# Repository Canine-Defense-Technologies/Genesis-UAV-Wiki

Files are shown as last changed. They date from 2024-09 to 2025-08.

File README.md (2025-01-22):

---
cover: .gitbook/assets/23155555555.png
coverY: 0
---

# Overview

## Genesis UAV

{% embed url="https://youtu.be/HFgrlNx3w98?feature=shared" %}

The merge between an FPV drone and a slow-moving high-endurance drone platform Genesis defines a new family of Tactical Utility Drones. The true balance of agility, speed, endurance, modularity, & manufacturability; Genesis is a new drone class. Built for serious U.S. civilians & defense professionals.

{% hint style="info" %}
Genesis drone family and all associated files on this wiki © 2025 by [Canine Defense Technologies ](https://www.k9defense.tech/)is licensed under [CC BY-SA 4.0](https://creativecommons.org/licenses/by-sa/4.0/?ref=chooser-v1)
{% endhint %}

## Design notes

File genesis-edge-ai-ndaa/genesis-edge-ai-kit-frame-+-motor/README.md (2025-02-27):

---
cover: ../../.gitbook/assets/P1170314.JPG
coverY: -83
---

# Genesis Edge AI Kit (Frame + Motor)

## Purchase Kit Here:

{% embed url="https://www.k9defense.tech/store/p/genesis-full-hardware-kit-j2g47-s429t-xrbjd" %}

<figure><figcaption></figcaption></figure>

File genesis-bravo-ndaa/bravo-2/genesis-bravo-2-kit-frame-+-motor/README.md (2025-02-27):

# Copy of Genesis Bravo 2 Kit (Frame + Motor)

## Purchase Kit Here:

{% embed url="https://www.k9defense.tech/store/p/genesis-full-hardware-kit-j2g47-s429t" %}

<figure><figcaption></figcaption></figure>

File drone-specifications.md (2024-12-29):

---
cover: .gitbook/assets/32467456.png
coverY: 0
---

# Drone Specifications

{% hint style="info" %}
The specifications will vary based on setup, motor selection, battery selection, frame type, etc. The metrics below should only be used for reference.&#x20;
{% endhint %}

| Stat | Value | Freedom Units |
| --- | --- | --- |
| Airframe Weight | 1.8 kg (Carbon Fiber)  | 2.2 lbs |
| Airframe Weight with Battery | 2.65 kg (Carbon Fiber) | 5.8 lbs |
| Blade Diameter | 15" \~ 20" | 15" \~ 20" |
| Flight Time | 15 \~ 40+ min | 15 \~ 40+ min |
| Max speed | 100+ km/hr | 62+ mph |
| Climb Rate | 16 m/sec | 35.7 mph |
| Thrust to Weight Ratio | 6.1/1 | 6.1/1 |
| Max Payload | 4 kg | 8.8 lbs |
| Do Not Exceed Payload | 5 kg | 11 lbs |
| Nominal Payload | 2 kg | 4.4 lbs |

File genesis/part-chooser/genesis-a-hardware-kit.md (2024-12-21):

---
cover: ../../.gitbook/assets/20241018_020027 (1).jpg
coverY: 0
---

# Genesis Hardware Kit (Archived)

{% hint style="warning" %}
As of Dec 2024, this page is stored for archival purposes. K9 is no longer offering this product.
{% endhint %}

## Purchase Kit Here:

{% embed url="https://www.k9defense.tech/store/p/genesis-hardware-kit" %}

We've made it a convenient kit with all the major hardware pre-labeled and sourced. The kit also includes the TPU landing gear, so you will only need to print the rest of the frame in one material.

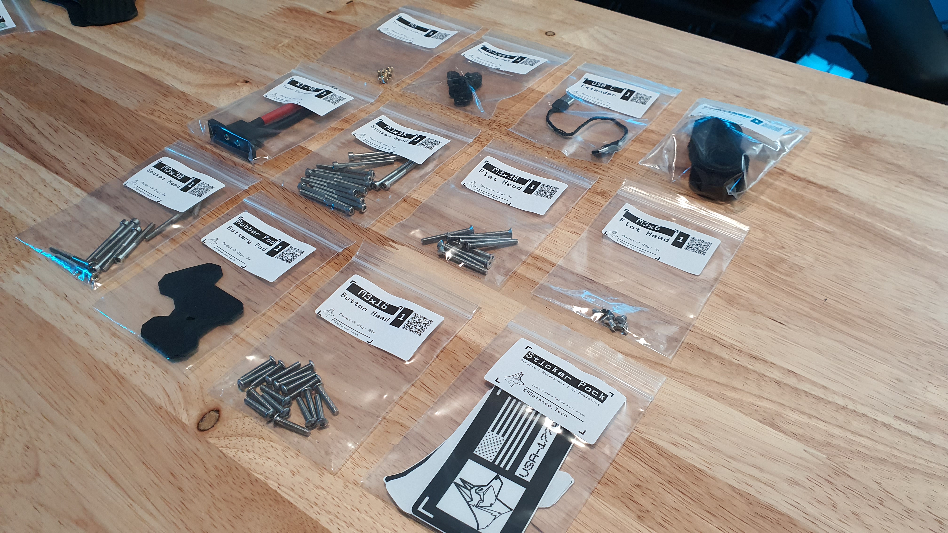
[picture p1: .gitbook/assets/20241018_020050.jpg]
<figure><figcaption></figcaption></figure>

{% hint style="info" %}
After purchasing the kit, ensure to source the additional parts.
{% endhint %}

## Additional Parts to Source:&#x20;

{% content-ref url="3d-printed-parts/" %}
[3d-printed-parts](3d-printed-parts/)
{% endcontent-ref %}

{% content-ref url="hardware/sheet-parts.md" %}
[sheet-parts.md](hardware/sheet-parts.md)
{% endcontent-ref %}

{% content-ref url="hardware/propellers.md" %}
[propellers.md](hardware/propellers.md)
{% endcontent-ref %}

{% content-ref url="hardware/arm-tubes.md" %}
[arm-tubes.md](hardware/arm-tubes.md)
{% endcontent-ref %}

{% content-ref url="electronics/" %}
[electronics](electronics/)
{% endcontent-ref %}

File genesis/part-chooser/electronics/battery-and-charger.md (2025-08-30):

---
cover: ../../../.gitbook/assets/1342234.png
coverY: 0
---

# Battery

{% hint style="warning" %}
As of April 2025, this page is stored for archival purposes. K9 has replaced the Genesis drone family to the newly improved Genesis Bravo 3.
{% endhint %}

### Reccomended Batteries:

| Part | Capacity  | C Rating | Link | Notes |
| --- | --- | --- | --- | --- |
| RDQ 6s | 6000 mah  | 100c | [Link](https://www.racedayquads.com/collections/6s-batteries/products/rdq-series-22-2v-6s-6000mah-100c-lipo-battery-xt90-anti-spark) | Best value. |
| Gens Ace 6s | 5500 mah  | 60c | [Link](https://genstattu.com/GA-B-60C-5500-6S1P-XT90S) | |
| Tattu G-Tech 6s | 11000 mah | 25c | [Link](https://genstattu.com/tattu-22-8-25c-6s-11000-mah-high-voltage-lipo-battery-with-xt90-s-plug-for-uav.html) | |

{% hint style="info" %}
When choosing alternative batteries, it is reccomended to use a 6S battery for Genesis. Ensure that there is a minimum C rating of 20c, and a minimum capacity of 3000 mah.&#x20;
{% endhint %}

### Battery Straps:

| Part | Link | Notes |
| --- | --- | --- |
| | [Link](https://www.racedayquads.com/collections/6s-batteries/products/rdq-series-22-2v-6s-6000mah-100c-lipo-battery-xt90-anti-spark) | Best value. |
| Gens Ace 6s | [Link](https://genstattu.com/GA-B-60C-5500-6S1P-XT90S) | |
| Tattu G-Tech 6s | [Link](https://genstattu.com/tattu-22-8-25c-6s-11000-mah-high-voltage-lipo-battery-with-xt90-s-plug-for-uav.html) | |

### Reccomended LiPo Fireproof Bags & Boxes:

{% hint style="warning" %}
Fireproof bags are **HIGHLY** recommended for charging and transporting LiPo batteries.
{% endhint %}

{% embed url="https://store.flitetest.com/flite-test-lipo-bag/" %}

{% embed url="https://store.flitetest.com/bat-safe-lipo-charging-box/" %}

### Learn more about choosing batteries for drones:

{% embed url="https://oscarliang.com/lipo-battery-guide/" %}

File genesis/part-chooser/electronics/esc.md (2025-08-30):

---
cover: ../../../.gitbook/assets/43543.png
coverY: 0
---

# ESC

{% hint style="warning" %}
As of April 2025, this page is stored for archival purposes. K9 has replaced the Genesis drone family to the newly improved Genesis Bravo 3.
{% endhint %}

ESCs or Electronic Speed Controllers are what drives the brushless DC motors on a drone. Genesis is designed to use any 30x30 4 in 1 ESC on the market. ESCs will determine the agility, flight performance, speed, and max payload of a drone. It's recommended to select an ESC with a total current rating higher than what is expected to be drawn. To make things easier, below are ESCs we recommend for your Genesis build.

## Recommended ESCs

<table><thead><tr><th>Name</th><th width="66">Link</th><th data-type="rating" data-max="5">Flight Performance</th><th>Notes</th></tr></thead><tbody><tr><td>ARK 4 in 1 ESC</td><td><a href="https://arkelectron.com/product/ark-4in1-esc/">Link</a></td><td>5</td><td>Based on AM32</td></tr></tbody></table>

## Other ESC Options

<table><thead><tr><th>Name</th><th width="65">Link</th><th data-type="rating" data-max="5">Flight Performance</th><th>Notes</th></tr></thead><tbody><tr><td>XRotor FPV G2 ESC</td><td><a href="https://www.brainfpv.com/product/xrotor-fpv-g2-esc-4in1-65a/">Link</a></td><td>4</td><td>Based on BLHeli</td></tr></tbody></table>

{% hint style="danger" %}
Select an ESC with a rating of **6s 50 Amps minimum**!&#x20;
{% endhint %}

**Learn more about selecting ESC for drones:**

{% embed url="https://oscarliang.com/esc/" %}

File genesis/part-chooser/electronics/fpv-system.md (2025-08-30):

---
cover: ../../../.gitbook/assets/8790435.png
coverY: 0
---

# FPV System

{% hint style="warning" %}
As of April 2025, this page is stored for archival purposes. K9 has replaced the Genesis drone family to the newly improved Genesis Bravo 3.
{% endhint %}

FPV (First Person View) allows the ability to stream low latency live video from the drone to give the pilot a direct view from onboard the drone. There are two types of FPV systems, Analog and Digital. Analog offers a simple and robust video transmission and is ubiquitously used and cross-compatible across all systems. One major downside to Analog is low video quality and the lack of security (Unencrypted video streams mean anyone with a video receiver can see your drone video feed). Digital systems offer HD video with more latency, higher cost, and locked system ecosystems. Learn more [below](fpv-system.md#setting-up-your-own-fpv-system). We have linked some analog systems that we have tested for the Genesis A.&#x20;

## Analog FPV System

### Recommended TX:

<table><thead><tr><th>Name</th><th data-type="rating" data-max="5">Performance</th><th>Link</th><th>Notes</th></tr></thead><tbody><tr><td>RDQ Mach 3</td><td>3</td><td><a href="https://www.racedayquads.com/collections/video-transmitters-antennas/products/rdq-mach-3-video-transmitter-25-1000mw-5-8ghz-vtx-choose-version">Link</a></td><td>Great budget option.</td></tr><tr><td>TBS Unify</td><td>5</td><td><a href="https://www.getfpv.com/tbs-unify-pro-5g8-hv-sma.html?utm_source=google&#x26;utm_medium=cpc&#x26;utm_campaign=DM+-+NB+-+PMax+-+Shop+-+No-index+-+SM+-+ALL+%7C+Full+Funnel&#x26;utm_content=pmax_x&#x26;utm_keyword=&#x26;utm_matchtype=&#x26;campaign_id=20799936859&#x26;network=x&#x26;device=c&#x26;gc_id=20799936859&#x26;gad_source=1&#x26;gclid=CjwKCAjw3624BhBAEiwAkxgTOlUY_xcNTtWX1cJEOJ5iW14ZB0qeFVxo0IYkRT4tzReWoJYRQwIEkRoCR4QQAvD_BwE">Link</a></td><td></td></tr></tbody></table>

### Recommended Antenna (Drone Side):

<table><thead><tr><th>Name</th><th data-type="rating" data-max="5">Performance</th><th>Link</th><th>Notes</th></tr></thead><tbody><tr><td>Lolipop 4</td><td>3</td><td><a href="https://www.amazon.com/Usmile-Lollipop-Antenna-Quadcopter-Transmitter/dp/B07T61ZJDP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;dib=eyJ2IjoiMSJ9.c5H9b4vWH4OifFzq9usEmtI5KkqhITzEmiD51_svO1v2b3I1hOy8nwFpmOyQGW8v-bgZgF88vuVuF30-0tTZP7VU8n_TUKAyG8TeqeHZ-YI5wMPeEapI6YgQjewlsoixLu5c97ZC9P23V9IlfPSNs91PvlJRfPSkqfXe8iXB128BdXRaUopNnwmyDsH1318mHBJm3N1yYnkZrmZGlXlKH6G9M_bhG0iigCUEtQaMtok.DY_RcYAx582_5yeRB7txUZGegIfkLyQ7kPeytWxOSrA&#x26;dib_tag=se&#x26;keywords=foxeer%2Bantenna&#x26;qid=1726022679&#x26;sprefix=foxeer%2Bantenna%2Caps%2C79&#x26;sr=8-3&#x26;th=1">Link</a></td><td>Great budget option with sufficient performance.</td></tr><tr><td>Pagoda Pro</td><td>4</td><td><a href="https://www.amazon.com/Foxeer-Pagoda-Antenna-Omnidirectional-Quadcopeter/dp/B07L3GB6TM">Link</a></td><td>Great upgrade from the Lolipop 4 at a decent price.</td></tr><tr><td>Double AXII 2</td><td>5</td><td><a href="https://www.getfpv.com/lumenier-double-axii-2-long-range-right-angle-5-8ghz-antenna-rhcp.html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">Link</a></td><td>Best performance, but expensive.</td></tr></tbody></table>

{% hint style="success" %}
Ensure the antenna polarization direction matches what you purchase for the ground side.
{% endhint %}

### Reccomended FPV Camera:

<table><thead><tr><th>Name</th><th data-type="rating" data-max="5">Performance</th><th>Link</th><th>Notes</th></tr></thead><tbody><tr><td>Foxeer Razer</td><td>3</td><td><a href="https://www.getfpv.com/foxeer-razer-mini-1200tvl-2-1mm-fpv-camera.html?vid=8867&#x26;utm_source=google&#x26;utm_medium=cpc&#x26;utm_campaign=DM+-+NB+-+PMax+-+Shop+-+SM+-+ALL+%7C+Full+Funnel&#x26;utm_content=pmax_x&#x26;utm_keyword=&#x26;utm_matchtype=&#x26;campaign_id=17881616054&#x26;network=x&#x26;device=c&#x26;gc_id=17881616054&#x26;gad_source=1&#x26;gclid=CjwKCAjw3624BhBAEiwAkxgTOrW54H6gZ_F8JJGrk-jLCQE_YzAgPK_5oNC5rSTgIdBQMQHoG4huZxoC-toQAvD_BwE">Link</a></td><td></td></tr><tr><td>RunCam Night Eagle 3</td><td>4</td><td><a href="https://www.getfpv.com/runcam-night-eagle-hd-fpv-camera.html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">Link</a></td><td>Excellent night vision performance. Note image is best in black and white.</td></tr></tbody></table>

### Setting up your own FPV system:

[https://oscarliang.com/fpv-system/](https://oscarliang.com/fpv-system/)

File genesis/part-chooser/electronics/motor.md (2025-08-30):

---
cover: ../../../.gitbook/assets/5555555555555.png
coverY: 0
---

# Motor

{% hint style="warning" %}
As of April 2025, this page is stored for archival purposes. K9 has replaced the Genesis drone family to the newly improved Genesis Bravo 3.
{% endhint %}

Motor Selection is critical in determining the flight performance of the final drone build. Generally heavier motors output more power at the cost of flight time, and higher RPM motors deliver greater power, agility, and speed at the cost of endurance. Choosing a motor is a careful balance in choosing, the best option for your target specifications. To make things easier, below are motors we recommend for your Genesis build that have been vetted or tested to suit the specifications the majority of users will be looking for.&#x20;

##

## Reccomended Motor Options:

<table><thead><tr><th>Name</th><th width="75">Link</th><th data-type="rating" data-max="5">Speed</th><th data-type="rating" data-max="5">Flight Time</th><th width="92">Prop Size</th><th>Notes</th></tr></thead><tbody><tr><td>KDE 4012XF-400Kv</td><td><a href="https://www.kdedirect.com/collections/uas-multi-rotor-brushless-motors/products/kde4012xf-400">Link</a></td><td>4</td><td>4</td><td>15-20 Inch</td><td>Reccomended for 4kg payloads.</td></tr><tr><td>SunnySky X3108S-900Kv</td><td><a href="https://sunnyskyusa.com/collections/xs-motors/products/sunnysky-x3108s-motors">Link</a></td><td>5</td><td>3</td><td>15 Inch</td><td>Motor for fastest build.</td></tr><tr><td>SunnySky V3508-700Kv</td><td><a href="https://sunnyskyusa.com/collections/v-motors/products/sunnysky-v3508-motor?variant=45705642191">Link</a></td><td>5</td><td>3</td><td>15-16 Inch</td><td></td></tr></tbody></table>

## Motor Options (Budget):

{% hint style="warning" %}
All the motors in the budget list are made in China. It is recommended to spend more money and invest in motors from U.S. companies
{% endhint %}

<table><thead><tr><th>Name</th><th width="103">Link</th><th data-type="rating" data-max="5">Speed</th><th data-type="rating" data-max="5">Flight Time</th><th>Prop Size</th><th>Notes</th></tr></thead><tbody><tr><td>Aerodrive Sk3 4240-740Kv</td><td><a href="https://hobbyking.com/en_us/turnigy-aerodrive-sk3-4240-740kv-brushless-outrunner-motor.html">Link</a></td><td>4</td><td>3</td><td>15-20 Inch</td><td>Reccomended motor out of the budget options.</td></tr><tr><td>Avian 4240-1000Kv</td><td><a href="https://amzn.to/3XLDeyR">Link</a></td><td>5</td><td>1</td><td>15 Inch</td><td>This motor is not reccomended for high endurance builds.</td></tr><tr><td>Propdrive 4238-750Kv</td><td><a href="https://hobbyking.com/en_us/propdrive-v2-4238-750kv-brushless-outrunner-motor.html">Link</a></td><td>4</td><td>3</td><td>15-18 Inch</td><td></td></tr><tr><td>Multistar 4224-610Kv</td><td><a href="https://hobbyking.com/en_us/turnigy-multistar-4225-610kv-16pole-multi-rotor-outrunner.html">Link</a></td><td>3</td><td>4</td><td>15 Inch</td><td></td></tr><tr><td>Flash Hobby 4215-650Kv</td><td><a href="https://amzn.to/4eKSK50">Link</a></td><td>3</td><td>4</td><td>15 Inch</td><td></td></tr><tr><td>Hobbyhh 4250-800Kv</td><td><a href="https://amzn.to/3ZMKehF">Link</a></td><td>4</td><td>2</td><td>15-20 Inch</td><td>This motor is heavy, not reccomended for most builds.</td></tr></tbody></table>

**Learn more about selecting motors for drones:**

{% hint style="info" %}
One unique capability of Genesis is its compatibility with model fixed-wing aircraft motors. This allows a larger selection of options for lower-cost high-power output motors typically not used on quadcopters.&#x20;
{% endhint %}

{% embed url="https://oscarliang.com/motors/" %}

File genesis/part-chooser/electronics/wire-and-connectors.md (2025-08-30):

---
cover: ../../../.gitbook/assets/54987646.png
coverY: 0
---

# Wire & Connectors

{% hint style="warning" %}
As of April 2025, this page is stored for archival purposes. K9 has replaced the Genesis drone family to the newly improved Genesis Bravo 3.
{% endhint %}

Selecting high-quality wires is critical in ensuring reliability and good performance in any drone build. The proper application of wire gauges and materials is an important variable in influencing the performance of the entire drone, so ensure that the proper gauges are applied. Though more expensive, silicone wire should be mandatory for any drone build to reduce the risk of fire. It is normal for the wires to get very hot during aggressive flight maneuvers, which can easily melt the exterior sheaths of most non silicone wires. To make things easier, below are wires we recommend for your Genesis build.

## Recommended Wires:

| Name | Link | Guage  | Notes |
| --- | --- | --- | --- |
| Ultra Thin Wire | [Link](https://www.amazon.com/stores/BNTECHGO/30GaugeSiliconeWire_SiliconeWire/page/0FB2C206-9F92-4DDF-8612-FECAFA318187) | 30 AWG | Use for signal and data lines. |
| Thin Wire | [Link](https://www.amazon.com/stores/BNTECHGO/24GaugeSiliconeWire_SiliconeWire/page/E1E31E64-1EAF-4459-8FFB-3448A42351AA) | 24 AWG | Use to provide low voltage power to accessories. |
| Medium Wire | [Link](https://www.amazon.com/BNTECHGO-Silicone-Flexible-Stranded-Impedance/dp/B06XS5N3HN) | 16 AWG | Use for motor wires. |
| Thick Wires | [Link](https://www.amazon.com/stores/BNTECHGO/10GaugeSiliconeWire_SiliconeWire/page/B3873000-8FFA-4D5A-BEDE-A2CAAAC2C6E5) | 10 AWG | Use for primary power lines between battery and ESC. |

{% hint style="danger" %}
Make sure to use **Silicone Wire** and check that the correct **gauge** wire is sourced.
{% endhint %}

## Connectors:

| Name | Link | Notes |
| --- | --- | --- |
| XT-90E-M | [Link](https://www.amazon.com/Yaohappy-XT90E-M-Mountable-Connector-Multicopter/dp/B09DBK97VJ) | For main battery connection. |
| USB C Breakout | [Link](https://www.amazon.com/ANMBEST-Connector-Receptacle-Adapter-Support/dp/B091CRLJM2) | |

{% hint style="danger" %}
Ensure battery connectors are purchased from the official manufacturer.
{% endhint %}

**Learn more about selecting wires and connectors for drones:**

{% embed url="https://oscarliang.com/wires-connectors/" %}

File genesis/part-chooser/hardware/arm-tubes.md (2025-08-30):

---
cover: ../../../.gitbook/assets/32412341.png
coverY: 0
---

# Arm Tubes

{% hint style="warning" %}
As of April 2025, this page is stored for archival purposes. K9 has replaced the Genesis drone family to the newly improved Genesis Bravo 3.
{% endhint %}

Genesis uses any common readily accessible 20mm (Outer Diameter) tube.

## Reccomended Materials:

<table><thead><tr><th>Material</th><th width="102">Link</th><th data-type="rating" data-max="5">Weight</th><th data-type="rating" data-max="5">Strength</th><th data-type="rating" data-max="5">Durability</th></tr></thead><tbody><tr><td>Alumnium (2mm)</td><td><a href="https://amzn.to/3XS4zzk">Link</a></td><td>5</td><td>4</td><td>5</td></tr><tr><td>Twill Weave Carbon Fiber (2mm wall thickness)</td><td><a href="https://amzn.to/47XlWn1">Link</a></td><td>2</td><td>5</td><td>3</td></tr></tbody></table>

{% hint style="info" %}
It is possible to substitute the arm tubes with other materials—experiment at your own risk.
{% endhint %}

## Reccomended Tube Length:

| Prop Width | Tube Length |
| --- | --- |
| 15-16 inch | 250 mm |
| 18-90 inch | 300 mm |
| 20-22 inch | 330 mm |

{% hint style="success" %}
Make sure to prepare 4 tubes of the same length. Specify the tube length for your [propeller ](propellers.md)selection.
{% endhint %}

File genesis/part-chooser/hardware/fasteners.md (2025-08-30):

---
cover: ../../../.gitbook/assets/3435.png
coverY: 0
---

# Fasteners

{% hint style="warning" %}
As of April 2025, this page is stored for archival purposes. K9 has replaced the Genesis drone family to the newly improved Genesis Bravo 3.
{% endhint %}

<table><thead><tr><th>Part</th><th width="118">Quantity</th><th width="140">Link</th><th>Mounting Area</th></tr></thead><tbody><tr><td>M3x30mm Flat Head</td><td>8x</td><td><a href="https://www.mcmaster.com/92125A140/">Link</a></td><td>Arm mount</td></tr><tr><td>M3x30mm Socket Head</td><td>8x</td><td><a href="https://www.mcmaster.com/91292A022/">Link</a></td><td>Motor mount</td></tr><tr><td>M3x35mm Socket Head</td><td>16x</td><td><a href="https://www.mcmaster.com/92290A763/">Link</a></td><td>Top assembly &#x26; motor mount</td></tr><tr><td>M3x6mm Flat Head</td><td>4x</td><td><a href="https://www.mcmaster.com/92125A126/">Link</a></td><td>XT-90 &#x26; FPV Camera Mount</td></tr><tr><td>M3x16mm Button Head</td><td>20x</td><td><a href="https://www.mcmaster.com/92095A184/">Link</a></td><td>Motor, electronics mount</td></tr><tr><td>M3 Nylon Lock Nut</td><td>36x</td><td><a href="https://www.mcmaster.com/93625A100/">Link</a></td><td>Bottom Fastener</td></tr><tr><td>M3 Threaded Insert</td><td>4x</td><td><a href="https://www.googleadservices.com/pagead/aclk?sa=L&#x26;ai=DChcSEwiHjamMwpmJAxWfSkcBHa_0PA0YABALGgJxdQ&#x26;ae=2&#x26;co=1&#x26;gclid=CjwKCAjwjsi4BhB5EiwAFAL0YLDzh-quFKZViITE91FhclWrvX84cer987slNAVIebOH1915PqxL0RoCWoUQAvD_BwE&#x26;ohost=www.google.com&#x26;cid=CAESV-D2yJGVkNPYhvhUOPEVP2xthTDzz58g7Ly9VbO4QFdvajcUMuz1ea1kes5BMYlmWUrgazzHIo7gzbZFH0Lt-gtgibgD6TvLMF2QRGO6VXbe8xuqP6sAsw&#x26;sig=AOD64_2K9rZmY0QN-z2FpDxjRIGQhSG90Q&#x26;q&#x26;adurl&#x26;ved=2ahUKEwiXhKOMwpmJAxXwKFkFHZ2KCqkQ0Qx6BAgQEAE">Link</a></td><td>XT-90 &#x26; FPV Camera Mount</td></tr><tr><td>M3 Washer</td><td>24x</td><td><a href="https://www.mcmaster.com/98689A112/">Link</a></td><td>Bottom Assembly</td></tr><tr><td>M-Lock Hardware Set</td><td>4X</td><td><a href="https://amzn.to/3Bmuh7u">Link</a></td><td>Battery/Payload Mount</td></tr></tbody></table>

{% hint style="success" %}
18-8 Stainless Steel is recommended for most of the fasteners as a balance of cost and durability. Ensure that the M3x35mm Socket Head screws are 316 Stainless Steel.&#x20;
{% endhint %}

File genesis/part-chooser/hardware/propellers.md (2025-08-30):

---
cover: ../../../.gitbook/assets/1233214.png
coverY: 0
---

# Propellers

{% hint style="warning" %}
As of April 2025, this page is stored for archival purposes. K9 has replaced the Genesis drone family to the newly improved Genesis Bravo 3.
{% endhint %}

Genesis can accommodate a diverse range of prop diameters. Wider props yield higher efficiency and thrust at a cost of speed and agility, tighter props yield higher speed and agility for a decrease in flight time.

## Recommended Props:

<table><thead><tr><th>Part</th><th>Diameter</th><th>Material</th><th data-type="rating" data-max="5">Thrust</th><th data-type="rating" data-max="5">Agility</th><th data-type="rating" data-max="5">Speed</th><th>Link</th></tr></thead><tbody><tr><td>Elo Nylon 15x</td><td>15 Inch</td><td>Nylon/CF reinforced</td><td>4</td><td>5</td><td>5</td><td><a href="https://sunnyskyusa.com/collections/polymer-propellers/products/eolo-cn15-5-5-prop">Link</a></td></tr><tr><td>Generic 15x5.5</td><td>15 Inch</td><td>Carbon Fiber</td><td>4</td><td>5</td><td>5</td><td><a href="https://amzn.to/3XRJYLs">Link</a></td></tr><tr><td>KDE-CF185-DP</td><td>18 Inch</td><td>Carbon Fiber</td><td>5</td><td>4</td><td>3</td><td><a href="https://www.kdedirect.com/collections/multi-rotor-propeller-blades/products/kde-cf185-dp">Link</a></td></tr><tr><td>Elo CF 18x</td><td>18 Inch</td><td>Carbon Fiber</td><td>5</td><td>4</td><td>4</td><td><a href="https://sunnyskyusa.com/collections/carbon-fiber-propellers/products/eolo-carbon-fiber-uav-propellers-18x6-5-inch">Link</a></td></tr></tbody></table>

{% hint style="warning" %}
Ensure the propeller diameter is paired with the optimal [motor](../electronics/motor.md) selection.
{% endhint %}

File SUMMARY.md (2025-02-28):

# Table of contents

* [Overview](README.md)
* [Drone Specifications](drone-specifications.md)

## Getting Started

* [Genesis UAV Variants](getting-started/genesis-uav-variants.md)

## Genesis

* [Part Chooser](genesis/part-chooser/README.md)
  * [Genesis Hardware Kit (Archived)](genesis/part-chooser/genesis-a-hardware-kit.md)
  * [Genesis Full Frame Kit (Archived)](genesis/part-chooser/genesis-a-full-frame-kit.md)
  * [3D Printed Parts](genesis/part-chooser/3d-printed-parts/README.md)
    * [Materials & Print Settings](genesis/part-chooser/3d-printed-parts/materials-and-print-settings.md)
    * [Genesis Digital FPV Main Body](genesis/part-chooser/3d-printed-parts/genesis-digital-fpv-main-body.md)
  * [Hardware](genesis/part-chooser/hardware/README.md)
    * [Sheet Parts](genesis/part-chooser/hardware/sheet-parts.md)
    * [Propellers](genesis/part-chooser/hardware/propellers.md)
    * [Arm Tubes](genesis/part-chooser/hardware/arm-tubes.md)
    * [Fasteners](genesis/part-chooser/hardware/fasteners.md)
  * [Electronics](genesis/part-chooser/electronics/README.md)
    * [Motor](genesis/part-chooser/electronics/motor.md)
    * [ESC](genesis/part-chooser/electronics/esc.md)
    * [Flight Controller](genesis/part-chooser/electronics/flight-controller.md)
    * [GPS](genesis/part-chooser/electronics/gps.md)
    * [FPV System](genesis/part-chooser/electronics/fpv-system.md)
    * [Radio & RC Receiver](genesis/part-chooser/electronics/radio-and-rc-receiver.md)
    * [Battery](genesis/part-chooser/electronics/battery-and-charger.md)
    * [Wire & Connectors](genesis/part-chooser/electronics/wire-and-connectors.md)
* [Genesis Assembly Manual](genesis/genesis-assembly-manual/README.md)
  * [1. Part Preparation](genesis/genesis-assembly-manual/1.-part-preparation.md)
  * [2. Arm Assembly](genesis/genesis-assembly-manual/2.-arm-assembly.md)
  * [3. Airframe Structure](genesis/genesis-assembly-manual/3.-airframe-structure.md)
  * [4. FPV, USB, & RX Electronics](genesis/genesis-assembly-manual/4.-fpv-usb-and-rx-electronics.md)
* [Genesis CAD File](genesis/genesis-cad-file.md)

## Genesis Bravo (NDAA)

* [Bravo](genesis-bravo-ndaa/fpv/README.md)
  * [Genesis Bravo FPV Kit (Archived)](genesis-bravo-ndaa/bravo/genesis-bravo-fpv-kit-archived.md)
  * [Kit Assembly Manual (Archived)](genesis-bravo-ndaa/bravo/kit-assembly-manual-archived/README.md)
    * [1. Part Prep & Unboxing](genesis-bravo-ndaa/bravo/kit-assembly-manual-archived/1.-part-prep-and-unboxing.md)
    * [2. FPV Cam Mount & Arm Brackets](genesis-bravo-ndaa/bravo/kit-assembly-manual-archived/2.-fpv-cam-mount-and-arm-brackets.md)
    * [3. Arm Integration and Alignment](genesis-bravo-ndaa/bravo/kit-assembly-manual-archived/3.-arm-integration-and-alignment.md)
    * [4. Electronics](genesis-bravo-ndaa/bravo/kit-assembly-manual-archived/4.-electronics.md)
    * [5. Final Frame Assembly](genesis-bravo-ndaa/bravo/kit-assembly-manual-archived/5.-final-frame-assembly.md)
    * [6. Battery Mount, Props, & Antenna Installation](genesis-bravo-ndaa/bravo/kit-assembly-manual-archived/6.-battery-mount-props-and-antenna-installation.md)
  * [BOM (Archived)](genesis-bravo-ndaa/bravo/bom-archived.md)
  * [Digital FPV (Archived)](genesis-bravo-ndaa/bravo/digital-fpv-archived.md)
  * [CAD File (Archived)](genesis-bravo-ndaa/bravo/cad-file-archived.md)
* [Bravo 2](genesis-bravo-ndaa/bravo-v2/README.md)
  * [Genesis Bravo 2 Kit (Frame + Motor)](genesis-bravo-ndaa/bravo-2/genesis-bravo-2-kit-frame-+-motor/README.md)
    * [Kit Assembly Manual](genesis-bravo-ndaa/bravo-2/genesis-bravo-2-kit-frame-+-motor/kit-assembly-manual/README.md)
      * [Kit Parts List](genesis-bravo-ndaa/bravo-2/genesis-bravo-2-kit-frame-+-motor/kit-assembly-manual/kit-parts-list.md)
      * [1. Introduction](genesis-bravo-ndaa/bravo-2/genesis-bravo-2-kit-frame-+-motor/kit-assembly-manual/1.-introduction.md)
      * [2. Mounting ARK Teseo & ARK FLOW](genesis-bravo-ndaa/bravo-2/genesis-bravo-2-kit-frame-+-motor/kit-assembly-manual/2.-mounting-ark-teseo-and-ark-flow.md)
      * [3. FPV Camera Mount](genesis-bravo-ndaa/bravo-2/genesis-bravo-2-kit-frame-+-motor/kit-assembly-manual/3.-fpv-camera-mount.md)
      * [4. PCB & Electronics Stack Insallation](genesis-bravo-ndaa/bravo-2/genesis-bravo-2-kit-frame-+-motor/kit-assembly-manual/4.-pcb-and-electronics-stack-insallation.md)
      * [5. Antenna Mount Installation](genesis-bravo-ndaa/bravo-2/genesis-bravo-2-kit-frame-+-motor/kit-assembly-manual/5.-antenna-mount-installation.md)
      * [6. Electronics Installation & Wiring](genesis-bravo-ndaa/bravo-2/genesis-bravo-2-kit-frame-+-motor/kit-assembly-manual/6.-electronics-installation-and-wiring.md)
      * [7. Arm Installation](genesis-bravo-ndaa/bravo-2/genesis-bravo-2-kit-frame-+-motor/kit-assembly-manual/7.-arm-installation.md)
      * [8. Battery Mount & Landing Gear](genesis-bravo-ndaa/bravo-2/genesis-bravo-2-kit-frame-+-motor/kit-assembly-manual/8.-battery-mount-and-landing-gear.md)
      * [9. Propeller Installation](genesis-bravo-ndaa/bravo-2/genesis-bravo-2-kit-frame-+-motor/kit-assembly-manual/9.-propeller-installation.md)
  * [Genesis Bravo 2 Kit (ARK Bundle)](genesis-bravo-ndaa/bravo-v2/page-1.md)
    * [Kit Assembly Manual](genesis-bravo-ndaa/bravo-2/genesis-bravo-2-kit-ark-bundle/kit-assembly-manual/README.md)
      * [Kit Parts List](genesis-bravo-ndaa/bravo-2/genesis-bravo-2-kit-ark-bundle/kit-assembly-manual/kit-parts-list.md)
      * [1. Introduction](genesis-bravo-ndaa/bravo-2/genesis-bravo-2-kit-ark-bundle/kit-assembly-manual/1.-introduction.md)
      * [2. Electronics Installation & Wiring](genesis-bravo-ndaa/bravo-2/genesis-bravo-2-kit-ark-bundle/kit-assembly-manual/2.-electronics-installation.md)
      * [3. Arm Installation](genesis-bravo-ndaa/bravo-2/genesis-bravo-2-kit-ark-bundle/kit-assembly-manual/3.-arm-installation.md)
      * [4. Battery Mount & Landing Gear](genesis-bravo-ndaa/bravo-2/genesis-bravo-2-kit-ark-bundle/kit-assembly-manual/4.-battery-mount-and-landing-gear.md)
      * [5. Propeller Installation](genesis-bravo-ndaa/bravo-2/genesis-bravo-2-kit-ark-bundle/kit-assembly-manual/5.-propeller-installation.md)
  * [Bravo 2 PCB Files](genesis-bravo-ndaa/bravo-v2/power-distribution-pcb.md)

## Genesis Edge AI (NDAA)

* [Genesis Edge AI Kit (Frame + Motor)](genesis-edge-ai-ndaa/genesis-edge-ai-kit-frame-+-motor/README.md)
  * [Kit Assembly Manual](genesis-edge-ai-ndaa/genesis-edge-ai-kit-frame-+-motor/kit-assembly-manual/README.md)
    * [Kit Parts List](genesis-edge-ai-ndaa/genesis-edge-ai-kit-frame-+-motor/kit-assembly-manual/kit-parts-list.md)
    * [1. Introduction](genesis-edge-ai-ndaa/genesis-edge-ai-kit-frame-+-motor/kit-assembly-manual/1.-introduction.md)
    * [2. PD Board & ESC Installation](genesis-edge-ai-ndaa/genesis-edge-ai-kit-frame-+-motor/kit-assembly-manual/2.-pd-board-and-esc-installation.md)
    * [3. ARK Flow & Camera Installation](genesis-edge-ai-ndaa/genesis-edge-ai-kit-frame-+-motor/kit-assembly-manual/3.-ark-flow-and-camera-installation.md)
    * [4. Final Electronics Wiring & Arm Installation](genesis-edge-ai-ndaa/genesis-edge-ai-kit-frame-+-motor/kit-assembly-manual/4.-final-electronics-wiring-and-arm-installation.md)
    * [5. Top Assembly & Arm Mounting](genesis-edge-ai-ndaa/genesis-edge-ai-kit-frame-+-motor/kit-assembly-manual/5.-top-assembly-and-arm-mounting.md)
    * [6. Landing Gear & Antenna Installation](genesis-edge-ai-ndaa/genesis-edge-ai-kit-frame-+-motor/kit-assembly-manual/6.-landing-gear-and-antenna-installation.md)
    * [7. Propeller Installation](genesis-edge-ai-ndaa/genesis-edge-ai-kit-frame-+-motor/kit-assembly-manual/7.-propeller-installation.md)
* [Edge AI CAD File](genesis-edge-ai-ndaa/edge-ai-cad-file.md)
* [Genesis Edge AI Kit (ARK Bundle)](genesis-edge-ai-ndaa/genesis-edge-ai-kit-ark-bundle/README.md)
  * [Kit Assembly Manual](genesis-edge-ai-ndaa/genesis-edge-ai-kit-ark-bundle/kit-assembly-manual/README.md)
    * [Kit Parts List](genesis-edge-ai-ndaa/genesis-edge-ai-kit-ark-bundle/kit-assembly-manual/kit-parts-list.md)
    * [Introduction](genesis-edge-ai-ndaa/genesis-edge-ai-kit-ark-bundle/kit-assembly-manual/introduction.md)
    * [1.](genesis-edge-ai-ndaa/genesis-edge-ai-kit-ark-bundle/kit-assembly-manual/1..md)
    * [2.](genesis-edge-ai-ndaa/genesis-edge-ai-kit-ark-bundle/kit-assembly-manual/2..md)
    * [3.](genesis-edge-ai-ndaa/genesis-edge-ai-kit-ark-bundle/kit-assembly-manual/3..md)
* [I/O Acess & Payload Mount](genesis-edge-ai-ndaa/i-o-acess-and-payload-mount.md)
* [Edge AI CAD Files](genesis-edge-ai-ndaa/edge-ai-cad-files.md)
* [Edge AI PCB Files](genesis-edge-ai-ndaa/edge-ai-pcb-files.md)
* [BOM](genesis-edge-ai-ndaa/bom.md)

## Software Setup & First Flight

* [Flight Software Setup](software-setup-and-first-flight/flight-software-setup/README.md)
  * [Getting Started with PX4](software-setup-and-first-flight/flight-software-setup/getting-started-with-px4.md)
  * [Motor & ESC Setup](software-setup-and-first-flight/flight-software-setup/motor-and-esc-setup.md)
  * [Final Checks](software-setup-and-first-flight/flight-software-setup/final-checks.md)
  * [Saftey Checks](software-setup-and-first-flight/flight-software-setup/saftey-checks.md)
  * [First Hover](software-setup-and-first-flight/flight-software-setup/first-hover.md)
  * [Tuning](software-setup-and-first-flight/flight-software-setup/tuning.md)

## Developer resource

* [ARK FLOW Enclosure](developer-resource/ark-flow-enclosure.md)
* [Genesis Payload Rail Standard](developer-resource/genesis-payload-rail-standard.md)
* [Genesis R\&D Payload Tray](developer-resource/genesis-r-and-d-payload-tray.md)
* [Extended Landing Gear](developer-resource/extended-landing-gear.md)

## Legal Info

* [License](legal-info/license.md)
* [Disclaimer](legal-info/disclaimer.md)

## Genesis Swarm Dev Kit (NDAA)

* [Page 2](genesis-swarm-dev-kit-ndaa/page-2.md)

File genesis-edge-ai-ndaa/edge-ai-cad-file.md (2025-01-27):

---
cover: ../.gitbook/assets/3456r.png
coverY: -156
---

# Edge AI CAD File

## License:

{% hint style="info" %}
Genesis Edge AI © 2025 by [Canine Defense Technologies ](https://www.k9defense.tech/)is licensed under [CC BY-SA 4.0](https://creativecommons.org/licenses/by-sa/4.0/?ref=chooser-v1)
{% endhint %}

## CAD File:

{% file src="../.gitbook/assets/Genesis Edge AI.step" %}

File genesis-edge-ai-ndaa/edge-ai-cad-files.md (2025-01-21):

---
hidden: true
---

# Edge AI CAD Files

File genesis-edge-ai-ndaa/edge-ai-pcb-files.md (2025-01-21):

---
hidden: true
---

# Edge AI PCB Files

{% hint style="warning" %}
This is a BOM for the entire drone. If you purchased a Genesis Edge AI Kit, please reference the Kit Parts List&#x20;
{% endhint %}

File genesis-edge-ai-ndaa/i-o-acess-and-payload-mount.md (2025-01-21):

---
hidden: true
---

# I/O Acess & Payload Mount

Genesis Edge AI comes with a built

## Overview Video&#x20;

## I/O Acess

There are 2 covers on Genesis Edge AI for easy I/O acess of the Ark Jetson PAB board.

## Payload Mount

The top of Gen

Top Payload Mount example:

Reference the Genesis Edge AI CAD Files for hardware development.

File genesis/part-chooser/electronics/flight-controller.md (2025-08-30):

---
cover: ../../../.gitbook/assets/ARK_FPV_Rev_1.0 (1).png
coverY: 0
---

# Flight Controller

{% hint style="warning" %}
As of April 2025, this page is stored for archival purposes. K9 has replaced the Genesis drone family to the newly improved Genesis Bravo 3.
{% endhint %}

The Flight Controller is the brain of the drone. It's important to choose a reputable flight controller to ensure long-term operational reliability. We've listed some popular and tested flight controllers to make your selection easier.&#x20;

##

## Recommended FC:

<table><thead><tr><th>Name</th><th width="65">Link</th><th data-type="rating" data-max="5">Reliability </th><th>Notes</th></tr></thead><tbody><tr><td>ARK FPV Controller</td><td><a href="https://arkelectron.com/product/ark-fpv-flight-controller/">Link</a></td><td>5</td><td>Made in the U.S.A and based on the reputable V6X.</td></tr></tbody></table>

## Other FC Options:

<table><thead><tr><th>Name</th><th width="68">Link</th><th data-type="rating" data-max="5">Reliability </th><th>Notes</th></tr></thead><tbody><tr><td>Brain FPV</td><td><a href="https://www.brainfpv.com/brainfpv-shop/">Link</a></td><td>5</td><td>Made in the U.S.A</td></tr><tr><td>SpeedyBee</td><td><a href="https://www.getfpv.com/speedybee-f405-v4-stack-f4-v4-fc-55a-blheli-s-esc-30x30.html?utm_source=google&#x26;utm_medium=cpc&#x26;utm_campaign=DM+-+NB+-+PMax+-+Shop+-+SM+-+ALL+%7C+Full+Funnel&#x26;utm_content=pmax_x&#x26;utm_keyword=&#x26;utm_matchtype=&#x26;campaign_id=17881616054&#x26;network=x&#x26;device=c&#x26;gc_id=17881616054&#x26;gad_source=1&#x26;gclid=Cj0KCQjwr9m3BhDHARIsANut04ZS7mn7e4nWbMTFz_903hGtkh_wxescO-QkI-GcATmySN554TAjRusaAlRIEALw_wcB">Link</a></td><td>3</td><td>Made in China. Cheap and accessible. Note reliabilty issues during testing.</td></tr></tbody></table>

#### Finding your own FC options:&#x20;

{% embed url="https://ardupilot.org/copter/docs/common-autopilots.html" %}

{% hint style="info" %}
Most F405-based flight controllers will work on Genesis. Ensure the mounting pattern is 30mmx30mm.
{% endhint %}

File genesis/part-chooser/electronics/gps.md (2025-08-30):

---
cover: ../../../.gitbook/assets/23143214.png
coverY: 0
---

# GPS

{% hint style="warning" %}
As of April 2025, this page is stored for archival purposes. K9 has replaced the Genesis drone family to the newly improved Genesis Bravo 3.
{% endhint %}

GPS is not strictly necessary, but it is a good feature to have. Adding GPS to Genesis allows autonomous flight, return to home, and loitering features. Genesis is compatible with any smaller to standard 25mm ceramic patch antenna-based GPS module standard for FPV drones. Below are some economical GPS options we have tested:

##

## Recommended GPS:

<table><thead><tr><th>Name</th><th>Link</th><th data-type="rating" data-max="5">Reliability </th><th>Notes</th></tr></thead><tbody><tr><td>M10Q</td><td><a href="https://www.racedayquads.com/products/foxeer-gps-m10q-250-gps-compass?currency=USD&#x26;variant=40182285107313&#x26;stkn=ed68f1cb6bdd&#x26;tw_source=google&#x26;tw_adid=283730783439&#x26;tw_campaign=1483163436&#x26;gad_source=1&#x26;gclid=CjwKCAjw3P-2BhAEEiwA3yPhwHHF_XRbPw7YPZGfLhM1r8CUWrvbB8PF-dQbCn2FwlkporCq9uuqfxoCWYcQAvD_BwE">Link</a></td><td>5</td><td>U-Blox chipset. Fast and reliable.</td></tr><tr><td>HLRC</td><td><a href="https://www.amazon.com/HGLRC-Module-UBLOX-Compatible-Racing/dp/B0BX65QZJ8">Link</a></td><td>3</td><td>Decent budget option. May be a little slow for GPS lock.</td></tr><tr><td>BN-220</td><td><a href="https://www.amazon.com/Navigation-Raspberry-Betaflight-Geekstory-Shipping/dp/B07PRDY6DS">Link</a></td><td>5</td><td>Fast satellite lock.</td></tr></tbody></table>

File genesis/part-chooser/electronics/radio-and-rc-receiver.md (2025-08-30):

---
cover: ../../../.gitbook/assets/43575667546.png
coverY: 0
---

# Radio & RC Receiver

{% hint style="warning" %}
As of April 2025, this page is stored for archival purposes. K9 has replaced the Genesis drone family to the newly improved Genesis Bravo 3.
{% endhint %}

The Radio and Receiver is what allows the control signals to be wireless sent to the drone. The Radio control link is one of the most critical systems for any drone build. We recommend investing in a good radio system early on in your drone builds to offer many years of reliable operation.

## ELRS

We highly recommend ELRS, an open-source drone radio control link ecosystem. ELRS offers cross-compatibility between different hardware manufacturers and frequent firmware upgrades for new software-defined feature upgrades. \

Learn more:

{% embed url="https://www.expresslrs.org" %}

## Radio Reciever (drone side)

### Reccomended Option

{% hint style="warning" %}
Radiomaster products are not NDAA compliant.
{% endhint %}

Diverity allows the RX to switch to the optimal antenna in real-time. Genesis is designed to hold 2 RX antennas for maximum performance.

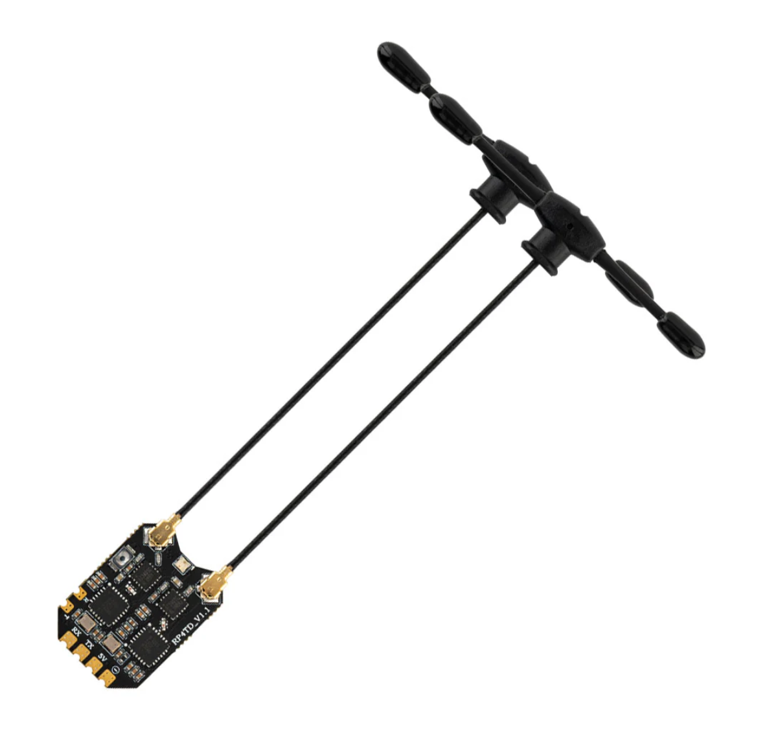
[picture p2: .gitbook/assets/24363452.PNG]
<figure><figcaption></figcaption></figure>

{% embed url="https://www.radiomasterrc.com/collections/rp-series-receivers/products/rp4td-expresslrs-2-4ghz-diversity-receiver" %}

## Radio Transmitter

{% hint style="warning" %}
Radiomaster products are not NDAA compliant
{% endhint %}

### Recommended Budget Option

The RadioMaster Pocket is a great beginner radio for getting started with drones.

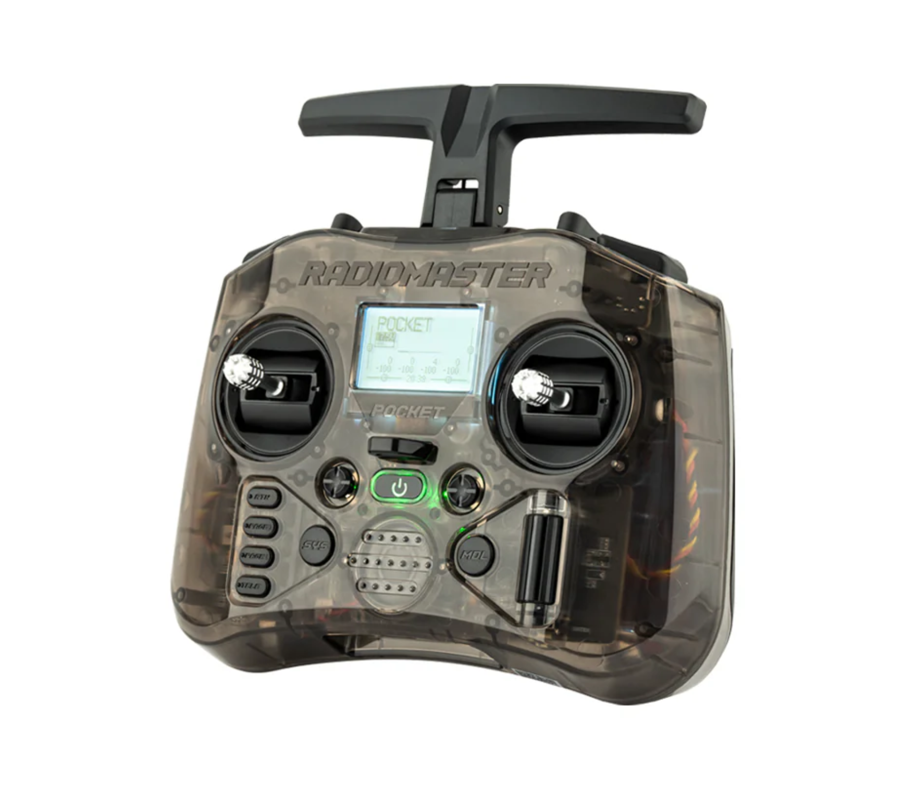
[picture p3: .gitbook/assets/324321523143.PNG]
<figure><figcaption></figcaption></figure>

{% embed url="https://www.radiomasterrc.com/products/pocket-radio-controller-m2" %}

{% hint style="info" %}
Ensure the ELRS version is selected.
{% endhint %}

### Recommended Option

The TX16 is a feature-dense option for advanced users. It is not recommended for beginners.

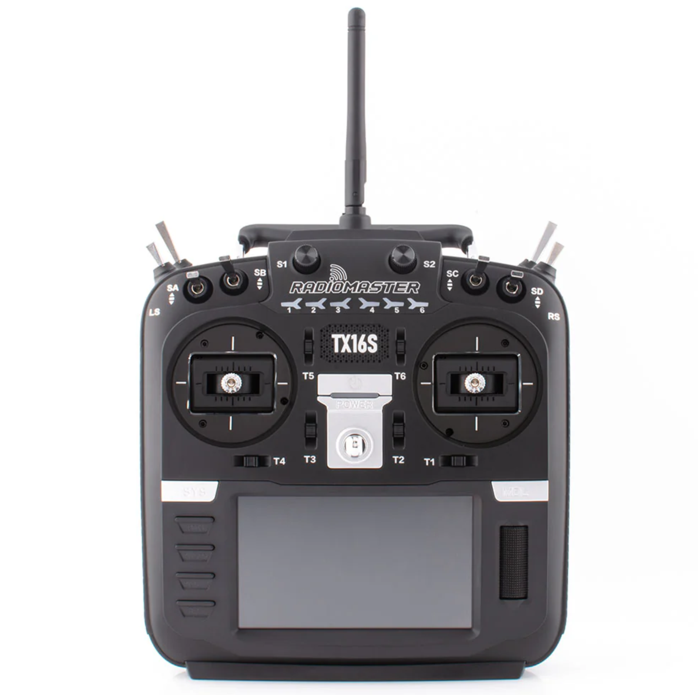
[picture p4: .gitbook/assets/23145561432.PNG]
<figure><figcaption></figcaption></figure>

{% embed url="https://www.radiomasterrc.com/products/tx16s-mark-ii-radio-controller?variant=42817741291751" %}

## Choosing Alternatives

{% embed url="https://oscarliang.com/radio-transmitter/" %}

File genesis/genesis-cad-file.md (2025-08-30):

---
cover: ../.gitbook/assets/23155555555.png
coverY: 0
---

# Genesis CAD File

{% hint style="warning" %}
As of April 2025, this page is stored for archival purposes. K9 has replaced the Genesis drone family to the newly improved Genesis Bravo 3.
{% endhint %}

## License:

{% hint style="info" %}
[Genesis UAV ](https://docs.k9defense.tech/v/genesis/)© 2025 by [Canine Defense Technologies ](https://www.k9defense.tech/)is licensed under [CC BY-SA 4.0](https://creativecommons.org/licenses/by-sa/4.0/?ref=chooser-v1)
{% endhint %}

## Genesis Analog FPV:

{% file src="../.gitbook/assets/Genesis FPV .step" %}

## Genesis Digital FPV:

{% file src="../.gitbook/assets/Genesis Digital FPV.step" %}

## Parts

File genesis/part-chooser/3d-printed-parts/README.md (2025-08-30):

---
cover: ../../../.gitbook/assets/43243254.png
coverY: 0
---

# 3D Printed Parts

{% hint style="warning" %}
As of April 2025, this page is stored for archival purposes. K9 has replaced the Genesis drone family to the newly improved Genesis Bravo 3.
{% endhint %}

Genesis is designed to use a variety of FDM printed parts optimized for accessible and economical desktop 3D printers. Ensure that mechanically adequate materials and print settings are selected before printing ([Materials & Print Settings](materials-and-print-settings.md)).

### Main Body

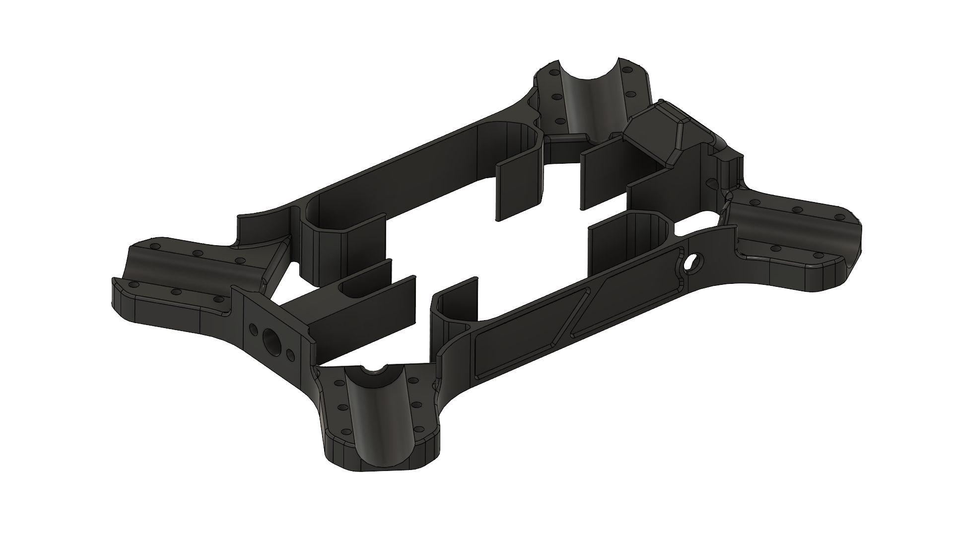
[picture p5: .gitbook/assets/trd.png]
<figure><figcaption></figcaption></figure>

#### Recommended Print Orientation:

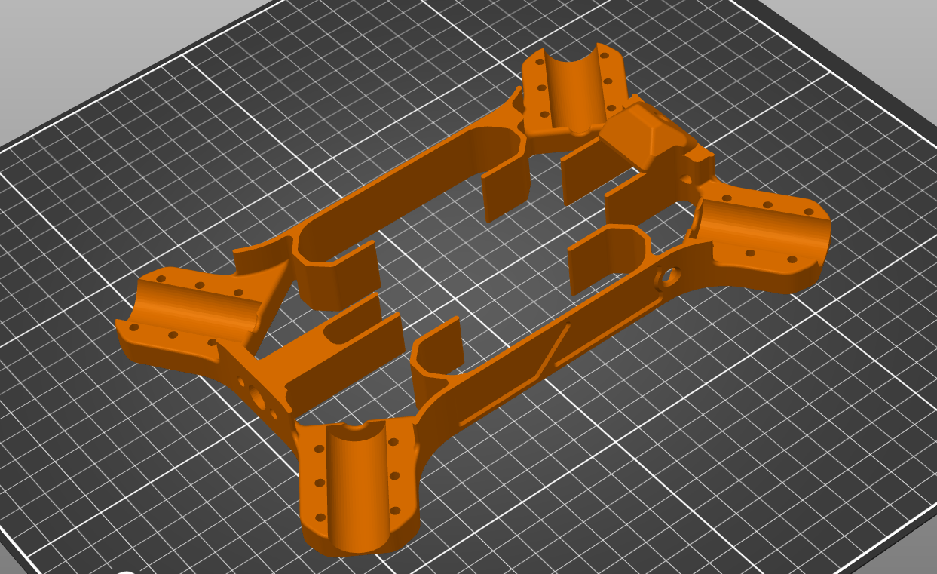
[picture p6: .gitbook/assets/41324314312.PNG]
<figure><figcaption></figcaption></figure>

#### Recommended Supports:

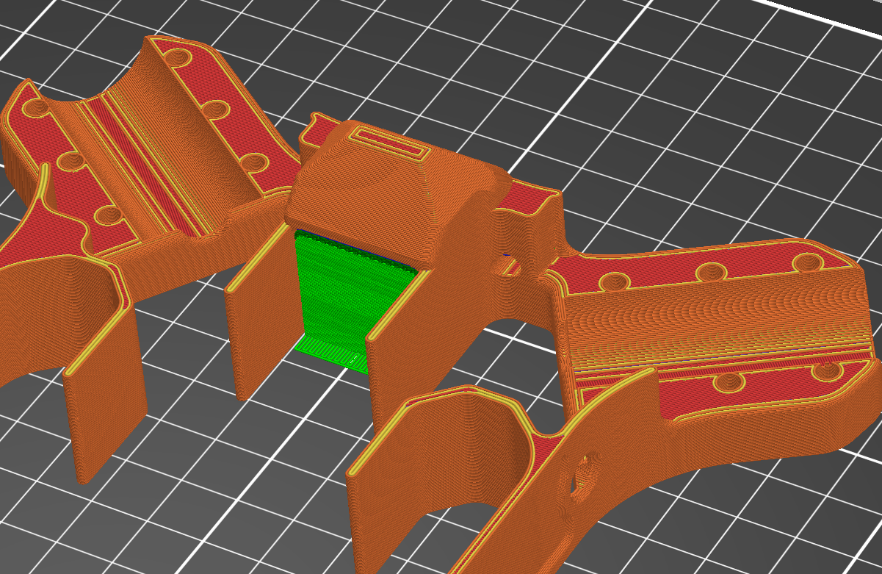
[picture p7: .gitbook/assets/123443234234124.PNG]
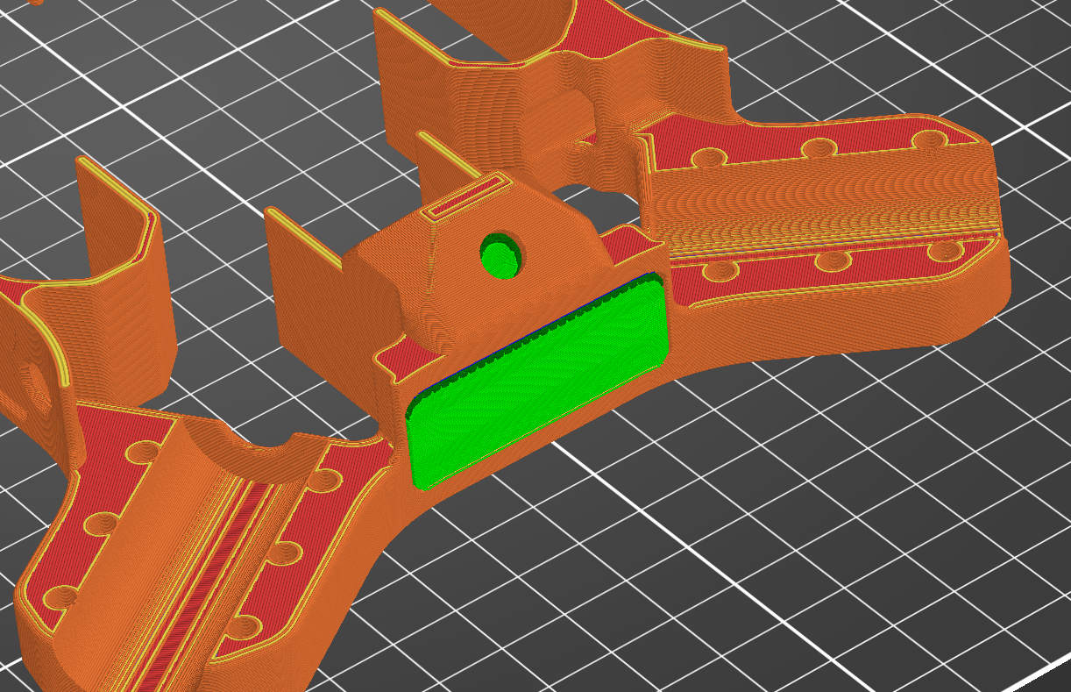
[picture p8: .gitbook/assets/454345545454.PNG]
<div><figure><figcaption></figcaption></figure> <figure><figcaption></figcaption></figure></div>

{% hint style="info" %}
For a Digital FPV build, do not print this file. Print the modified main body [**here**](genesis-digital-fpv-main-body.md).
{% endhint %}

{% file src="../../../.gitbook/assets/Genesis Main Body.3mf" %}

### Top Plate

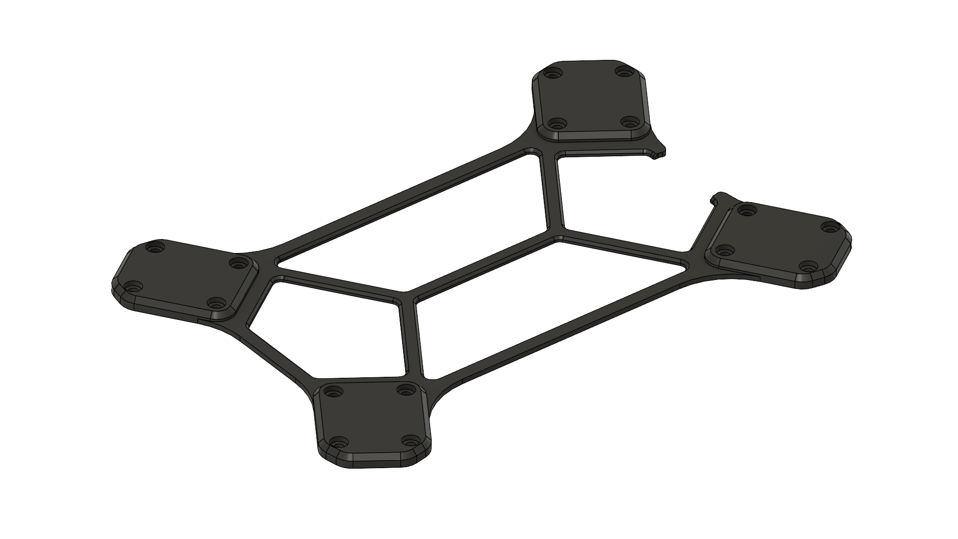
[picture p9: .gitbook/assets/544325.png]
<figure><figcaption></figcaption></figure>

#### Recommended Print Orientation:

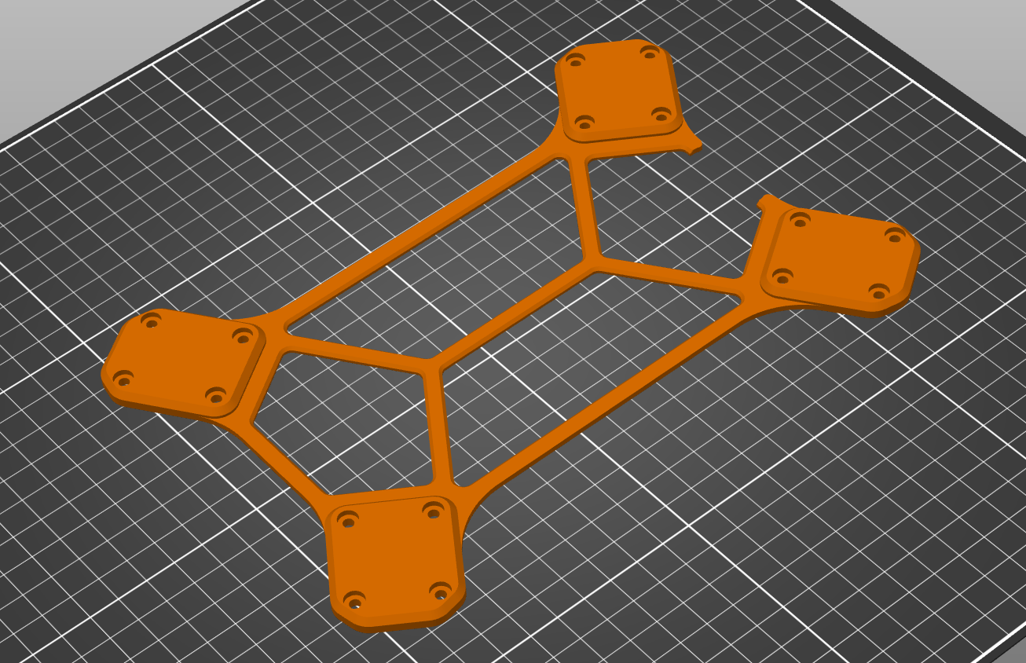
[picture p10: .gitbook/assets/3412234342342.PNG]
<div data-full-width="false"><figure><figcaption></figcaption></figure></div>

{% hint style="success" %}
No supports are needed.
{% endhint %}

{% file src="../../../.gitbook/assets/Genesis Top Plate.3mf" %}

###

### Arm Bracket

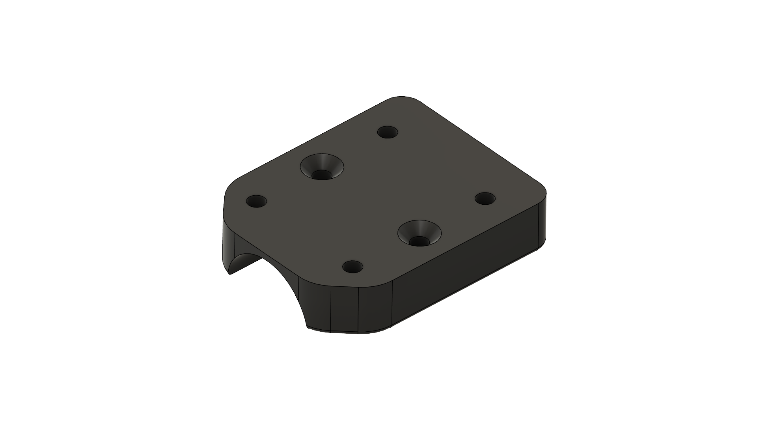
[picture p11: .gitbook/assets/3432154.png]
<figure><figcaption></figcaption></figure>

#### Recommend Print Orientation:

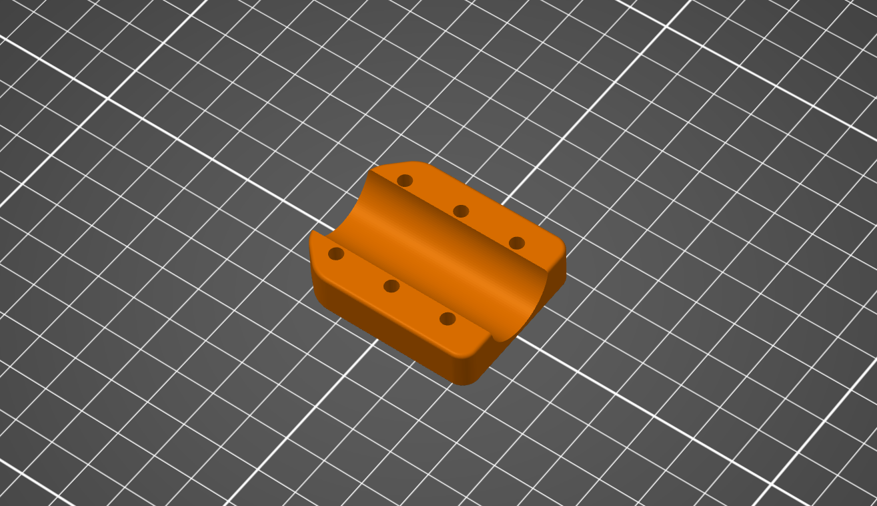
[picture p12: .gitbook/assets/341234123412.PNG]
<figure><figcaption></figcaption></figure>

{% hint style="success" %}
No supports are needed. Ensure 4 brackets are printed.
{% endhint %}

{% file src="../../../.gitbook/assets/Genesis Arm Mount.3mf" %}

###

### Motor Mount

<figure><figcaption></figcaption></figure>

#### Recommend Print Orientation:

<figure><figcaption></figcaption></figure>

#### Recommended Supports:

<figure><figcaption></figcaption></figure>

{% hint style="success" %}
Ensure 4 brackets are printed.&#x20;
{% endhint %}

{% file src="../../../.gitbook/assets/Genesis Motor Mount.3mf" %}

###

### Landing Gear

<figure><figcaption></figcaption></figure>

#### Recommended Print Orientation:

<figure><figcaption></figcaption></figure>

{% hint style="success" %}
No supports are needed. Ensure 4 brackets are printed. Make sure to print using flexible material like TPU.
{% endhint %}

{% file src="../../../.gitbook/assets/Genesis Landing Gear (1).3mf" %}

###

### FPV Camera Mount

<figure><figcaption></figcaption></figure>

#### Recommend Print Orientation:

<figure><figcaption></figcaption></figure>

{% file src="../../../.gitbook/assets/Genesis FPV Camera Mount.3mf" %}

### Battery Mount

<figure><figcaption></figcaption></figure>

#### Recommended Print Orientation:

<figure><figcaption></figcaption></figure>

#### Recommended Supports:

<figure><figcaption></figcaption></figure>

{% hint style="success" %}
Ensure 2 battery mounts are printed. Ensure to use 100% infill.
{% endhint %}

{% file src="../../../.gitbook/assets/Battery Mount (2).3mf" %}

### Rubber Stencil Tool

<figure><figcaption></figcaption></figure>

#### Recommended Print Orientation

<figure><figcaption></figcaption></figure>

{% hint style="success" %}
No supports are needed.
{% endhint %}

{% file src="../../../.gitbook/assets/Rubber Stencil Tool.3mf" %}

### Arm Alignment Tool

<figure><figcaption></figcaption></figure>

#### Recommended Print Orientation:

<figure><figcaption></figcaption></figure>

{% hint style="success" %}
No supports are needed. Ensure 4 Aligners are printed.
{% endhint %}

{% file src="../../../.gitbook/assets/Arm Alignment Tool.3mf" %}

##

## Printed Parts Checklist

| Part | Quantity | Material | Support | Recommended Infill |
| --- | --- | --- | --- | --- |
| Main Body | 1x | PLA, ASA, PETG | Yes | 15-60% |
| Top Plate | 1x | PLA, ASA, PETG | No | 15-25% |
| Arm Bracket | 4x | PLA, ASA, PETG | No | 25-70% |
| Motor Mount | 4x | PLA, ASA, PETG | Yes | 25-70% |
| Landing Gear | 4x | TPU, FLEX | No | 15% |
| FPV Camera Mount | 1x | PLA, ASA, PETG | No | 70% |
| Battery Mount | 2x | PLA, ASA, PETG | No | 70% |
| Rubber Stencil Tool | 1x | PLA, ASA, PETG | No | 15-100% |
| Arm Alignment Tool  | 4x | PLA | No | 15% |

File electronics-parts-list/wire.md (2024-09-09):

---
cover: ../.gitbook/assets/54987646.png
coverY: 0
---

# Wire-

Selecting high-quality wires is critical in ensuring reliability and good performance in any drone build. The proper application of wire gauges and materials is an important variable in influencing the performance of the entire drone, so ensure that the proper gauges are applied. Though more expensive, silicone wire should be mandatory for any drone build to reduce the risk of fire. It is normal for the wires to get very hot during aggressive flight maneuvers, which can easily melt the exterior sheaths of most nonsilicone wires. To make things easier, below are wires we recommend for your Genesis build.

## Recommended Wires for Genesis:

| Name | Link | Guage  | Notes |
| --- | --- | --- | --- |
| Ultra Thin Wire | [Link](https://www.amazon.com/stores/BNTECHGO/30GaugeSiliconeWire\_SiliconeWire/page/0FB2C206-9F92-4DDF-8612-FECAFA318187) | 30 AWG | Use for signal and data lines. |
| Thin Wire | [Link](https://www.amazon.com/stores/BNTECHGO/24GaugeSiliconeWire\_SiliconeWire/page/E1E31E64-1EAF-4459-8FFB-3448A42351AA) | 24 AWG | Use to provide low voltage power to accesories. |
| Medium Wire | [Link](https://www.amazon.com/BNTECHGO-Silicone-Flexible-Stranded-Impedance/dp/B06XS5N3HN) | 16 AWG | Use for motor wires. |
| Thick Wires | [Link](https://www.amazon.com/stores/BNTECHGO/10GaugeSiliconeWire\_SiliconeWire/page/B3873000-8FFA-4D5A-BEDE-A2CAAAC2C6E5) | 10 AWG | Use for primary power lines between battery and ESC. |

{% hint style="danger" %}
Make sure to use **Silicone Wire** and check that the correct **gauge** wire is used to reduce the **risk of fire**!
{% endhint %}

**Learn more about selecting wires for drones:**

{% embed url="https://oscarliang.com/wires-connectors/" %}

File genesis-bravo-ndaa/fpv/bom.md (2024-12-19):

# BOM

## Hardware

<table><thead><tr><th>Part</th><th width="118">Quantity</th><th width="140">Link</th><th>Mounting Area</th></tr></thead><tbody><tr><td>M3x30mm Flat Head</td><td>8x</td><td><a href="https://www.mcmaster.com/92125A140/">Link</a></td><td>Arm mount</td></tr><tr><td>M3x30mm Socket Head</td><td>8x</td><td><a href="https://www.mcmaster.com/91292A022/">Link</a></td><td>Motor mount</td></tr><tr><td>M3x35mm Socket Head</td><td>16x</td><td><a href="https://www.mcmaster.com/92290A763/">Link</a></td><td>Top assembly &#x26; motor mount</td></tr><tr><td>M3x8mm Flat Head</td><td>4x</td><td><a href="https://www.mcmaster.com/92125A128/">Link</a></td><td>XT-90 &#x26; FPV Camera Mount</td></tr><tr><td>M3x16mm Button Head</td><td>20x</td><td><a href="https://www.mcmaster.com/92095A184/">Link</a></td><td>Motor, electronics mount</td></tr><tr><td>M2x12mm Button Head</td><td>4x</td><td><a href="https://www.mcmaster.com/92095A455/">Link</a></td><td>Ark GPS Mount</td></tr><tr><td>M3 Pem Nut</td><td>36x</td><td><a href="https://www.mcmaster.com/94100A110/">Link</a></td><td>Electronics Mount, C Bracket, Motor Thrust Plate</td></tr><tr><td>M-Lock Hardware Set</td><td>4X</td><td><a href="https://www.midwayusa.com/product/1024196946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;pid=938140">Link</a></td><td>Battery/Payload Mount</td></tr></tbody></table>

## Electronics

| Name | Quantity | Link | Notes |
| --- | --- | --- | ----- |
| ARK FPV Flight Controller | 1x | [Link](https://arkelectron.com/product/ark-fpv-flight-controller/) | |
| ARK 4 in 1 ESC | 1x | [Link](https://arkelectron.com/product/ark-4in1-esc/) | |
| ARK GPS | 1x | [Link](https://arkelectron.com/product/ark-gps/) | |

## Motors

{% hint style="info" %}
Choose one of the three motor options below:
{% endhint %}

<table><thead><tr><th>Name</th><th width="75">Link</th><th data-type="rating" data-max="5">Speed</th><th data-type="rating" data-max="5">Flight Time</th><th width="92">Prop Size</th><th>Notes</th></tr></thead><tbody><tr><td>KDE 4012XF-400Kv</td><td><a href="https://www.kdedirect.com/collections/uas-multi-rotor-brushless-motors/products/kde4012xf-400">Link</a></td><td>4</td><td>4</td><td>15-20 Inch</td><td>Recommended for heavy payloads.</td></tr><tr><td>KDE3510XF-715Kv</td><td><a href="https://www.kdedirect.com/collections/uas-multi-rotor-brushless-motors/products/kde3510xf-715">Link</a></td><td>5</td><td>4</td><td>15 Inch</td><td>Recommended for most builds.</td></tr></tbody></table>

## NDAA Compliant RC System

| Name | Part | Link | Notes |
| --- | --- | --- | ----- |
| Orqa FPV.Ctrl | RC TX Handset | [Link](https://www.getfpv.com/commercial-industry-drones/ndaa-compliant/orqa-fpv-ctrl-radio-controller.html) | |
| Ghost Uber Lite | RC TX Unit (pair with the Orqa FPV.Ctrl | [Link](https://shop.orqafpv.com/products/immersionrc-immersionrc-ghost-uberlite-tx-module) | |

## NDAA Compliant FPV System

| Name | Part | Link | Notes |
| --- | --- | --- | ----- |
| Ghost Hybrid V2 | Analog FPV and RC RX combo | [Link](https://shop.orqafpv.com/products/immersionrc-immersionrc-ghost-hybrid-v2-uno) | |
| ORQA FPV.One PILOT FPV | Analog FOV goggles | [Link](https://www.getfpv.com/orqa-fpv-one-pilot-fpv-goggles.html) | |

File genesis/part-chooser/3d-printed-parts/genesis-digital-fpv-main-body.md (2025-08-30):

# Genesis Digital FPV Main Body

{% hint style="warning" %}
As of April 2025, this page is stored for archival purposes. K9 has replaced the Genesis drone family to the newly improved Genesis Bravo 3.
{% endhint %}

The Digital FPV configuration is identical except for the main body and camera mount print. The Digital FPV configuration main body hosts a dual antenna mount and a 20mm x 20mm mounting hole for the digital FPV VTX. The Digital FPV build is for advanced builders, the default Analog FPV configuration for Genesis is recommended for beginners.&#x20;

<figure><figcaption></figcaption></figure>

## Main Body (Digital FPV Mod)

<figure><figcaption></figcaption></figure>

### Recommended Print Orientation:

<figure><figcaption></figcaption></figure>

### Recommended Supports:

<div><figure><figcaption></figcaption></figure> <figure><figcaption></figcaption></figure></div>

{% file src="../../../.gitbook/assets/Genesis Main Body Digital FPV.3mf" %}

## FPV Camera Mount (Digital FPV Mod)

<figure><figcaption></figcaption></figure>

### Recommended Print Orientation:

<figure><figcaption></figcaption></figure>

### Recommended Supports:

<figure><figcaption></figcaption></figure>

{% file src="../../../.gitbook/assets/Digital FPV Camera Mount.3mf" %}

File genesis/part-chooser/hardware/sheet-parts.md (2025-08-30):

---
cover: ../../../.gitbook/assets/43123412341.png
coverY: 0
---

# Sheet Parts

{% hint style="warning" %}
As of April 2025, this page is stored for archival purposes. K9 has replaced the Genesis drone family to the newly improved Genesis Bravo 3.
{% endhint %}

Genesis uses a sheet material airframe structure to form a strong rigid sandwich airframe structure that is easy to mass produce economically and quickly. The airframe can be made out of either aluminum or carbon fiber, allowing the user to choose between durability or performance.

## Selecting Material

<table><thead><tr><th>Material</th><th data-type="rating" data-max="5">Weight</th><th data-type="rating" data-max="5">Strength</th><th data-type="rating" data-max="5">Durability</th></tr></thead><tbody><tr><td>5052-H32 Alumnium (2mm)</td><td>4</td><td>3</td><td>5</td></tr><tr><td>Twill Weave Carbon Fiber (2mm)</td><td>2</td><td>4</td><td>2</td></tr></tbody></table>

##

## Sheet Part List

### Airframe Top

<figure><figcaption></figcaption></figure>

{% file src="../../../.gitbook/assets/Airframe Top.dxf" %}

{% file src="../../../.gitbook/assets/Airframe Top.step" %}

###

### Airframe Bottom

<figure><figcaption></figcaption></figure>

{% file src="../../../.gitbook/assets/Airframe Bottom.dxf" %}

{% file src="../../../.gitbook/assets/Airframe Bottom.step" %}

###

### Motor Thrust Plate

<figure><figcaption></figcaption></figure>

{% hint style="success" %}
Ensure to cut 4 thrust plates.
{% endhint %}

{% file src="../../../.gitbook/assets/Motor Thrust Plate.dxf" %}

{% file src="../../../.gitbook/assets/Motor Thrust Plate.step" %}

##

## Recommended Cut Service

### Aluminum:&#x20;

Fast, affordable, and precise, RMFG is our go-to service for aluminum components.

{% embed url="https://www.rmfg.com" %}

### Carbon Fiber:

CNC Madness is a well-known and reputable carbon fiber cut service popular with drone hobbyists.&#x20;

{% embed url="https://cncmadness.com" %}

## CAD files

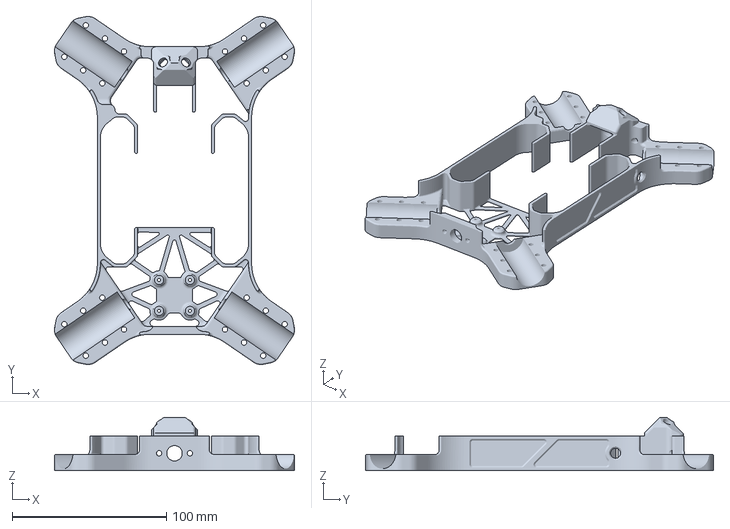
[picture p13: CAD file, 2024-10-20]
.gitbook/assets/Genesis Main Body Digital FPV.3mf
155.5 x 225.4 x 34.5 mm

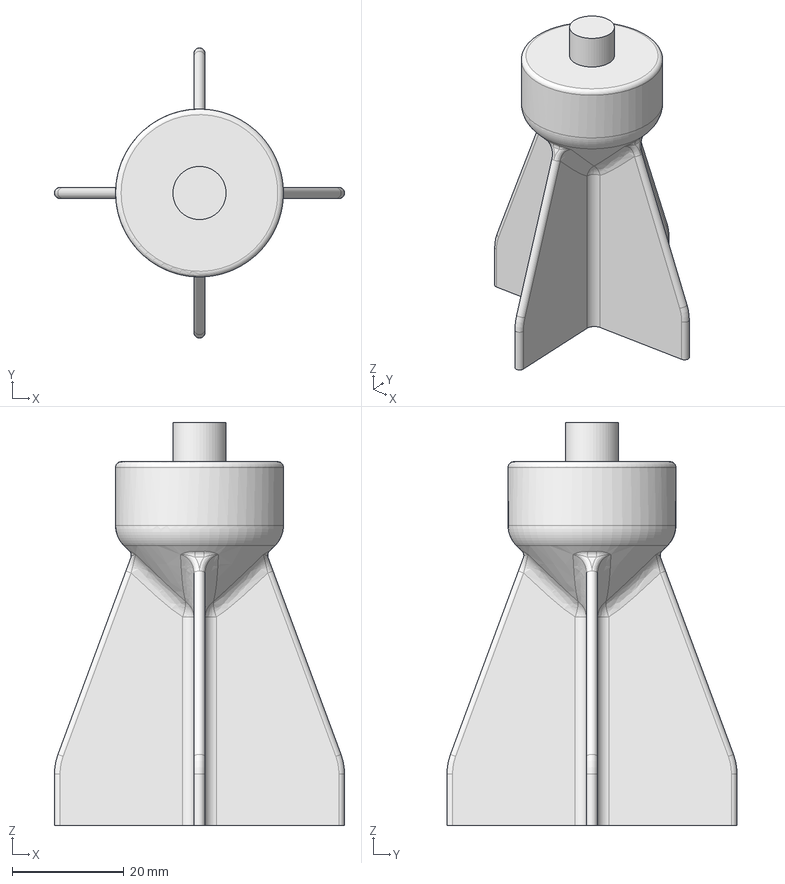
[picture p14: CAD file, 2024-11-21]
.gitbook/assets/arm alignment tool v2.step
51.8 x 51.8 x 72.0 mm

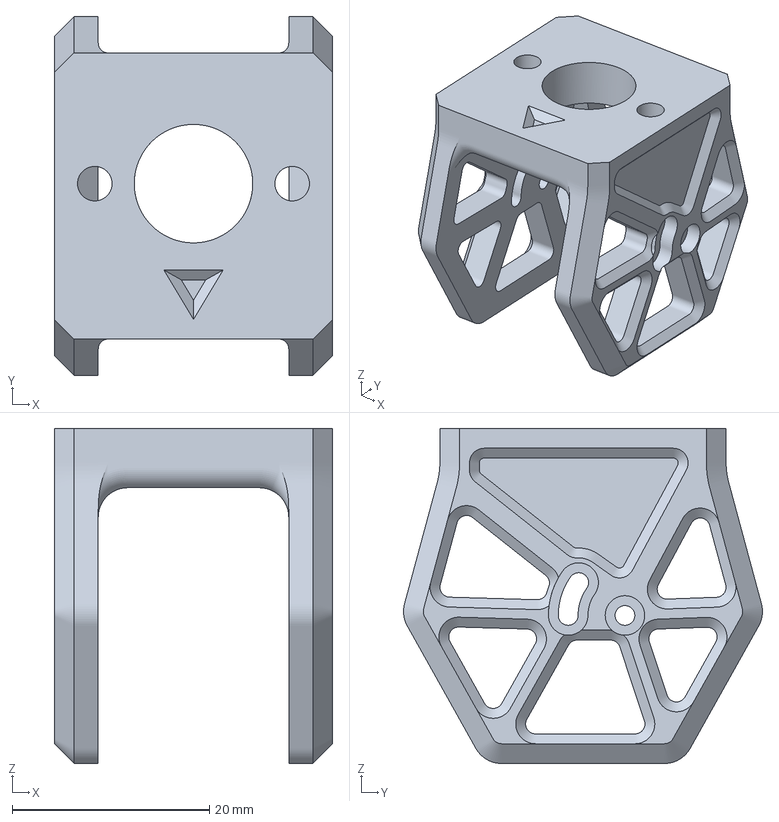
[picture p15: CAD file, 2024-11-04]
.gitbook/assets/Digital FPV Camera Mount.3mf
28.2 x 36.4 x 33.9 mm

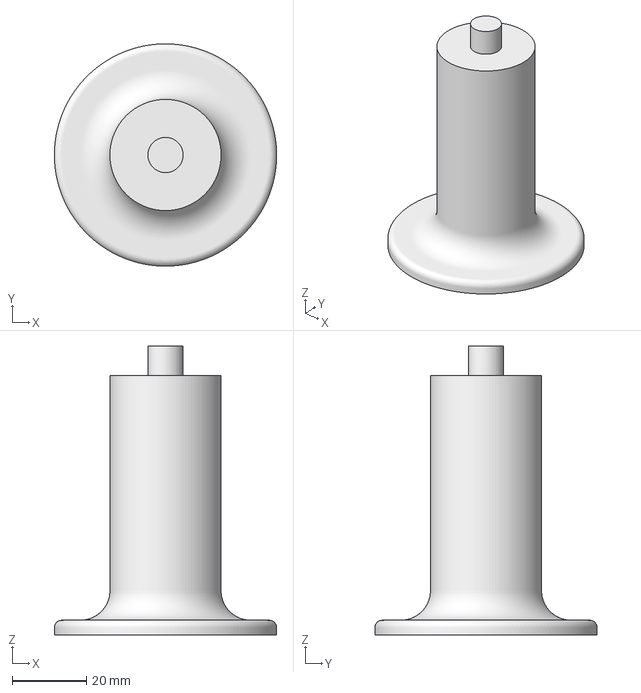
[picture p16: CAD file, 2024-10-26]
.gitbook/assets/Arm Alignment Tool.3mf
60.0 x 60.0 x 78.0 mm

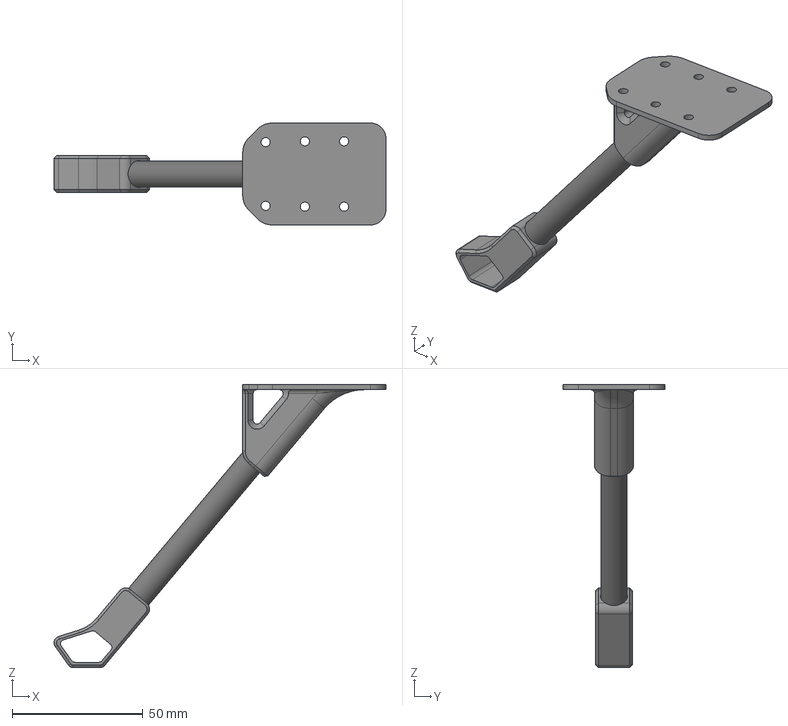
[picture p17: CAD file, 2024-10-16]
.gitbook/assets/Landing Gear Extended v1.step
127.0 x 39.0 x 108.3 mm

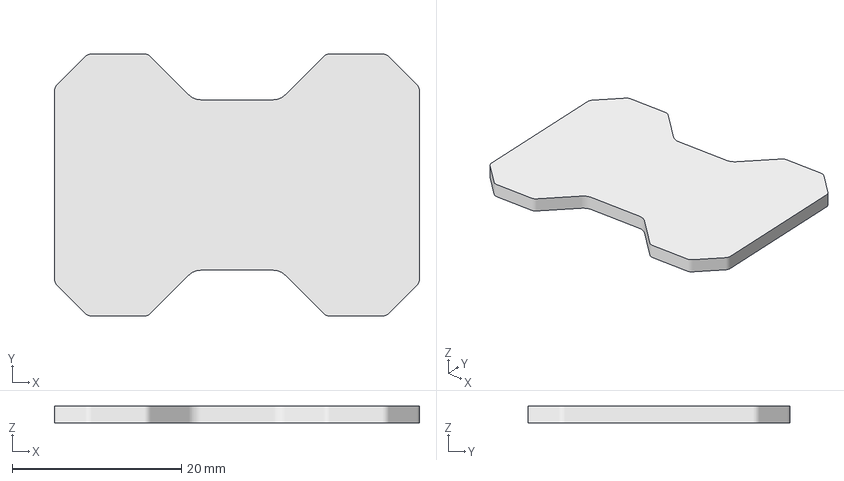
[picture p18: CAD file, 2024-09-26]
.gitbook/assets/Rubber Stencil Tool.3mf
43.2 x 31.0 x 2.00 mm

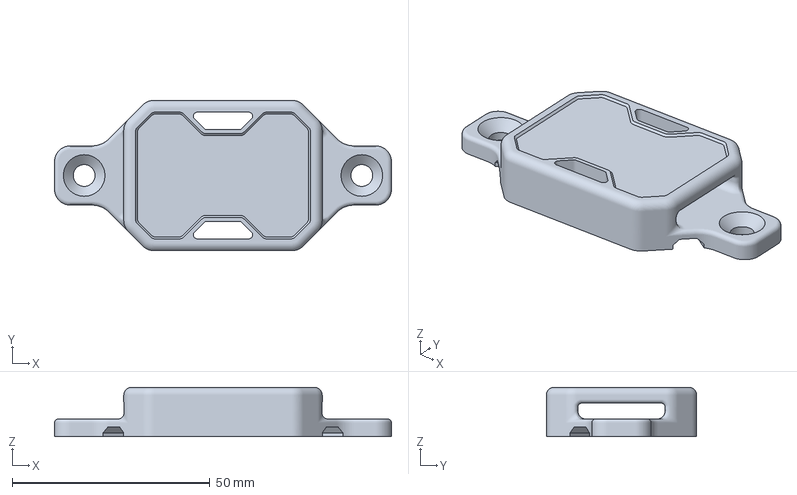
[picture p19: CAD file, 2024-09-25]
.gitbook/assets/Battery Mount.3mf
85.2 x 38.0 x 12.5 mm

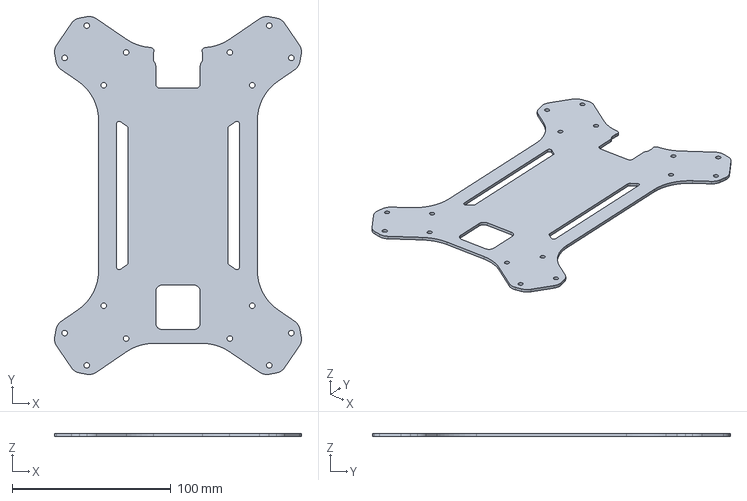
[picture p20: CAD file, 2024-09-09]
.gitbook/assets/Airframe Top.step
155.5 x 225.4 x 2.00 mm

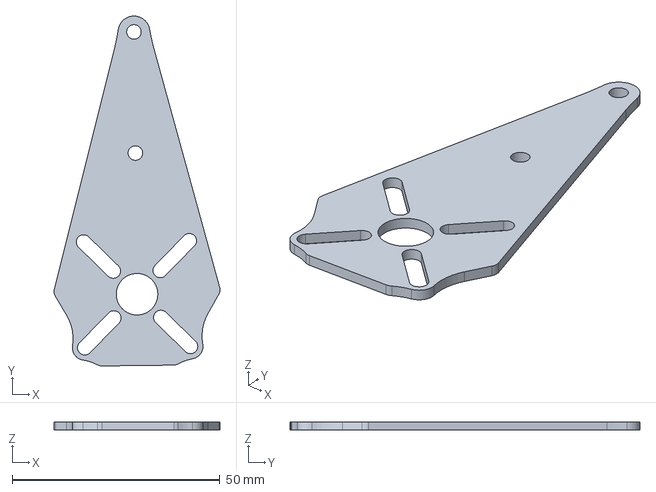
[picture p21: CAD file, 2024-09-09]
.gitbook/assets/Motor Thrust Plate.step
40.0 x 84.3 x 2.00 mm

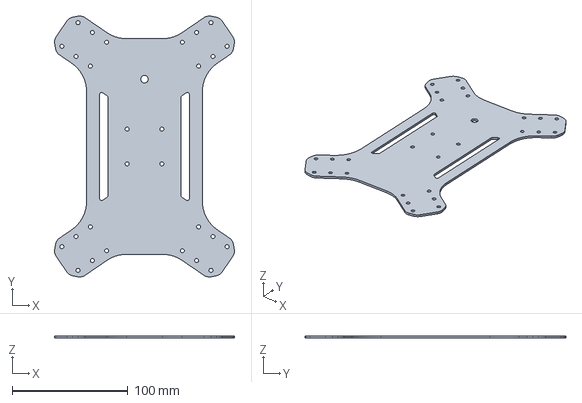
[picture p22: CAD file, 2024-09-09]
.gitbook/assets/Airframe Bottom.step
155.5 x 225.4 x 2.00 mm

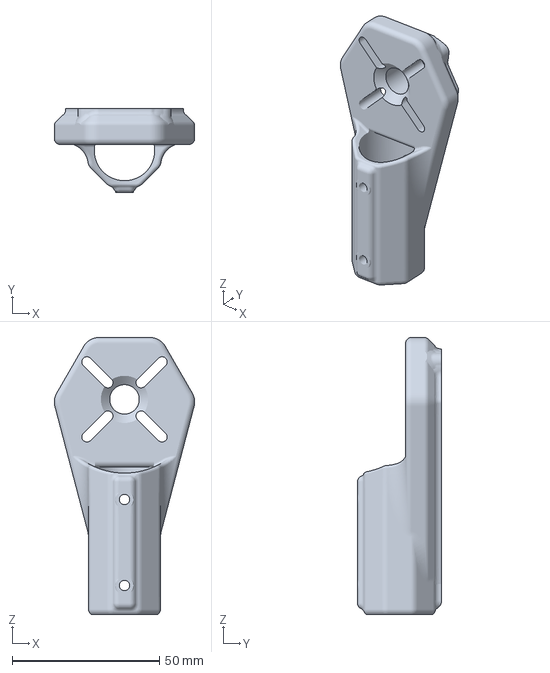
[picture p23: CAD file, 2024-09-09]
.gitbook/assets/Genesis Motor Mount.3mf
47.6 x 28.5 x 94.0 mm

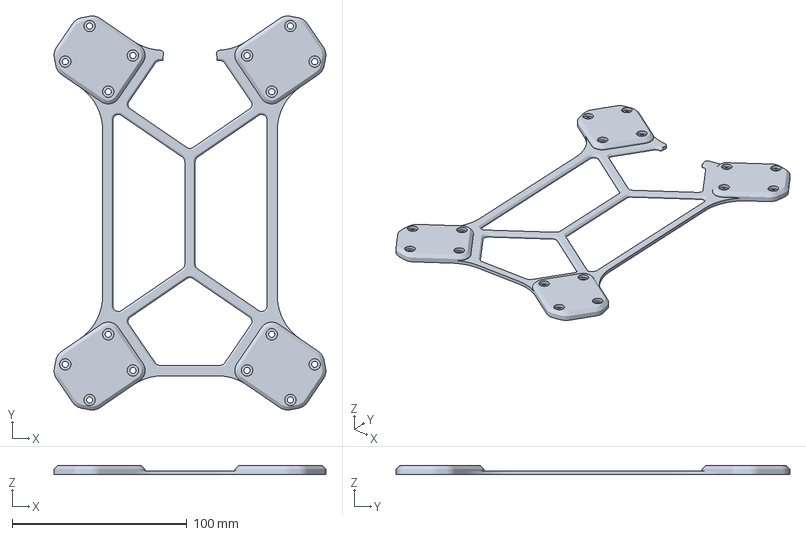
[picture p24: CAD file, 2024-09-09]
.gitbook/assets/Genesis Top Plate.3mf
155.5 x 225.4 x 5.00 mm

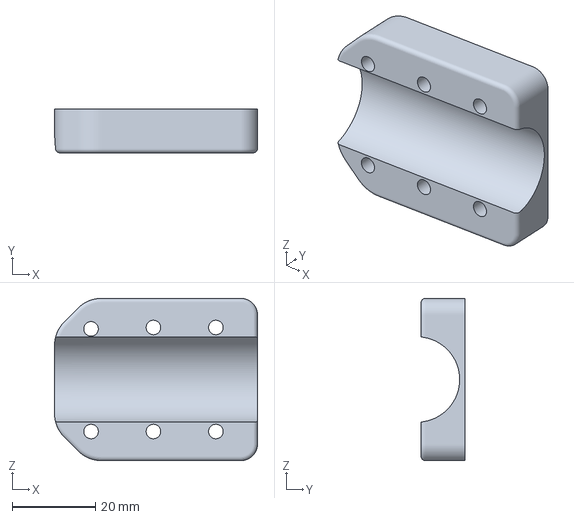
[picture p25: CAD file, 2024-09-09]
.gitbook/assets/Genesis Arm Mount.3mf
48.8 x 10.5 x 39.0 mm

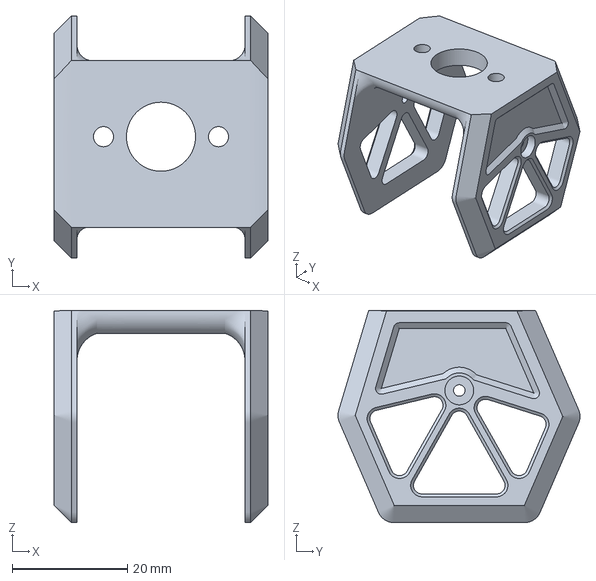
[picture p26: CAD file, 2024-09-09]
.gitbook/assets/Genesis FPV Camera Mount.3mf
37.2 x 42.1 x 36.9 mm

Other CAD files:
.gitbook/assets/Genesis Main Body.3mf
.gitbook/assets/Genesis Landing Gear.3mf
.gitbook/assets/Battery Mount (2).3mf
.gitbook/assets/Battery Mount (1).3mf
.gitbook/assets/Airframe Bottom.dxf
.gitbook/assets/Airframe Top.dxf
.gitbook/assets/Arm Alignment Tool (1).3mf
.gitbook/assets/Genesis Landing Gear (1).3mf
.gitbook/assets/Motor Thrust Plate.dxf

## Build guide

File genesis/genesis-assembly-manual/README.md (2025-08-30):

---
cover: ../../.gitbook/assets/P1170211.JPG
coverY: -158.72307692307692
---

# Genesis Assembly Manual

{% hint style="warning" %}
As of April 2025, this page is stored for archival purposes. K9 has replaced the Genesis drone family to the newly improved Genesis Bravo 3.
{% endhint %}

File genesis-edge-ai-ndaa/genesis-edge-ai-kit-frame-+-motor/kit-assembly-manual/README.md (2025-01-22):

---
cover: ../../../.gitbook/assets/3456r.png
coverY: -89.1076923076923
---

# Kit Assembly Manual

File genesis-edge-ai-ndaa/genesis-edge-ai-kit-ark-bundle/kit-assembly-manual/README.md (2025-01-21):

---
cover: ../../../.gitbook/assets/3456r.png
coverY: 0
---

# Kit Assembly Manual

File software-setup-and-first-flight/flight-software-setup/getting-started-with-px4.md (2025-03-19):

---
hidden: true
---

# Getting Started with PX4

ARK Jetson PAB&#x20;

ROTATION\_PITCH\_180\_YAW\_90

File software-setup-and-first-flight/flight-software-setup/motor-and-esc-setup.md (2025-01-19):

---
hidden: true
---

# Motor & ESC Setup

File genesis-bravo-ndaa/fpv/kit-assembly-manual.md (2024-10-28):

# Kit Assembly Manual

## Section 1: Unboxing

{% embed url="https://youtu.be/d0Ezix0-eI8" %}

## Section 2:&#x20;

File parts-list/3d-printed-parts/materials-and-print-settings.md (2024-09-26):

---
cover: ../../.gitbook/assets/Prusa i3 MK3S.png
coverY: 0
---

# Materials & Print Settings-

## Recommended Print Settings:

| Print Setting | Setting Parameter | Notes |
| --- | --- | --- |
| Layer Height | 0.2 or 0.15 mm | Do not exceed 0.2 mm layer height. |
| Infill | 15% or 100% | Do not go lower than 15% infill. Higher infill is reccomended for durability. |
| Infill Geomtry | Grid or Gyroid | |
| Perimeter Layers | 2 minimum | |

## Recommended Materials:

| Material | Notes |
| --- | --- |
| PLA + | Not recommended for high heat environments. |
| ABS | |
| PETG | Use high infill. |
| PC | |

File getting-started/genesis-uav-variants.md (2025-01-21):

---
cover: ../.gitbook/assets/3421431324 (1).png
coverY: 0
---

# Genesis UAV Variants

The Genesis drone family comes in three variants. Select the variant that matches your application or mission set below.

## Genesis

<figure><figcaption></figcaption></figure>

Genesis is the most economical, manufacturable, and accessible option for beginner drone builders. Genesis is easy to build with very few tools or resources required. Being electronics agnostic, users can select and source various motors, flight controllers, and more from a diverse range of suppliers. Genesis is designed to be simple, reliable, and accessible.

{% hint style="info" %}
Genesis is the most economical option and is recommended for most builders.
{% endhint %}

### Links:

#### [Genesis Docs](../genesis/part-chooser/)&#x20;

## Genesis Bravo (NDAA Compliant)

<figure><figcaption></figcaption></figure>

The Bravo model is for both civilian and defense professionals powered exclusively by [ARK Electronics](https://arkelectron.com).&#x20;

### Links:

#### [Genesis Bravo Docs ](../genesis-bravo-ndaa/fpv/)

#### [Buy Kits](https://www.k9defense.tech/store/p/genesis-full-hardware-kit-j2g47-s429t)

## Genesis-M (NDAA Compliant, Munition)

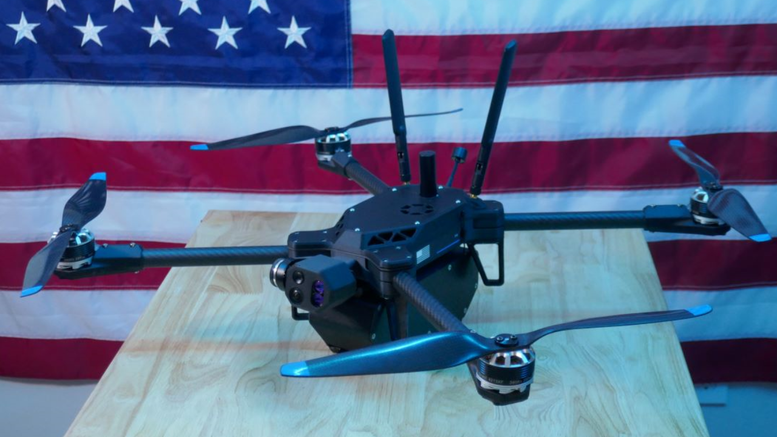
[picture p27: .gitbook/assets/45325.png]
<figure><figcaption></figcaption></figure>

The Genesis-M is designed for terminal guidance applications, cUAS, tactical ISR, and other multi-mission roles. Genesis-M is in active development for government customers. Genesis-M is only available for government and military customers. For details on procurement or development, please reach out to us.&#x20;

### Links:

#### [Contact Us](https://www.k9defense.tech)

## Genesis Edge AI

<figure><figcaption></figcaption></figure>

The fastest way to develop and deploy tactical AI on the edge, Genesis Edge AI was designed specifically for defense developers. Genesis Edge AI can support drone swarm development, tactical sensor tests, edge AI field experiments, and more.

### Links:

#### [Genesis Edge AI Docs](genesis-uav-variants.md#genesis-edge-ai)

#### [Buy Kits](https://www.k9defense.tech/store/p/genesis-full-hardware-kit-j2g47-s429t-xrbjd)

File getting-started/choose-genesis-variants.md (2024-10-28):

---
cover: ../.gitbook/assets/3421431324 (1).png
coverY: 0
---

# Choose Genesis Variants

The Genesis drone family comes in three variants. Select the variant that matches your application or mission set below.

## Genesis

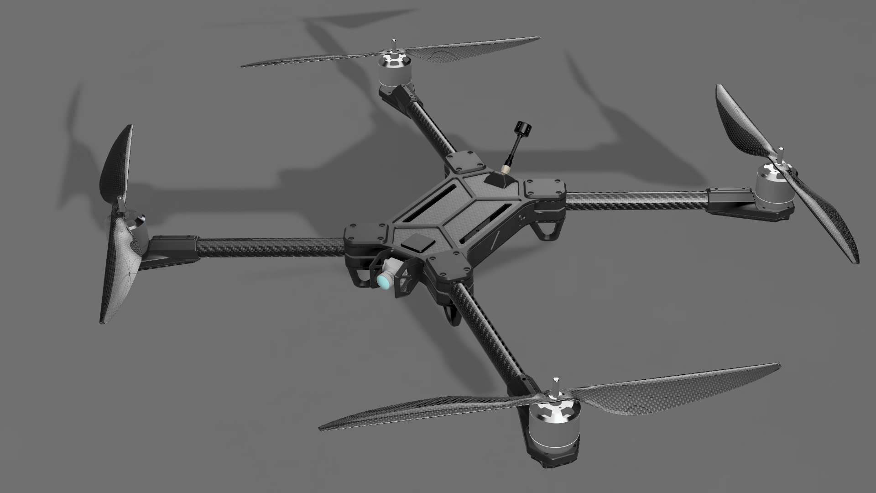
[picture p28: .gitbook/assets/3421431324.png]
<figure><figcaption></figcaption></figure>

Genesis is the most economical, manufacturable, and accessible variant of aimed for beginner drone builders. Genesis is easy to build with very few tools or resources required. Being electronics agnostic, users can select and source various motors, flight controllers, and more from a diverse range of suppliers. Genesis is designed to be simple, reliable, and accessible.

{% hint style="info" %}
Genesis is the most economical option and is recommended for most builders.
{% endhint %}

### Links:

#### [Genesis Docs](../genesis/part-chooser/)&#x20;

#### Buy Kits

## Genesis Bravo (NDAA Compliant)

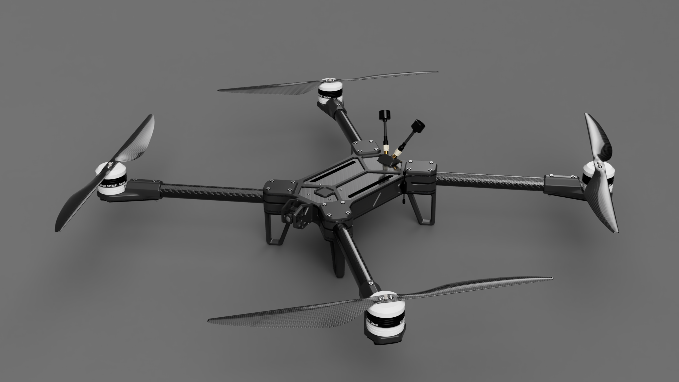
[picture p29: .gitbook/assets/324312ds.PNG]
<figure><figcaption></figcaption></figure>

The Bravo model is for both civilian and defense professionals powered exclusively by ARK Electronics.&#x20;

### Links:

#### [Genesis ](../genesis/part-chooser/)Bravo Docs&#x20;

#### Buy Kits

## Genesis-M (NDAA Compliant, Munition)

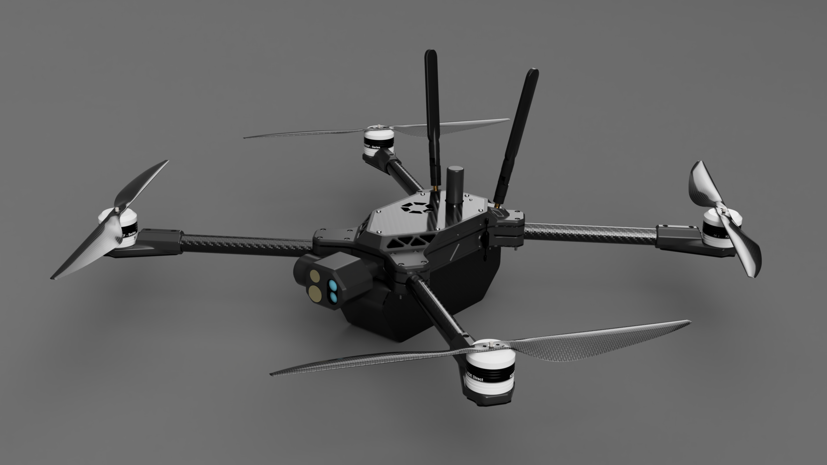
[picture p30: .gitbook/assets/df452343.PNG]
<figure><figcaption></figcaption></figure>

The Genesis-M is designed for terminal guidance applications, tactical ISR, and other multi-mission roles. Genesis-M is in active developing for government customers. Genesis-M is only available for government and military customers. For details on procurement or development, please reach out to us.&#x20;

### Links:

#### [Contact Us](https://www.k9defense.tech)

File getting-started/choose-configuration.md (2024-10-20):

---
hidden: true
---

# Choose Configuration

Genesis&#x20;

## Analog FPV (Default)

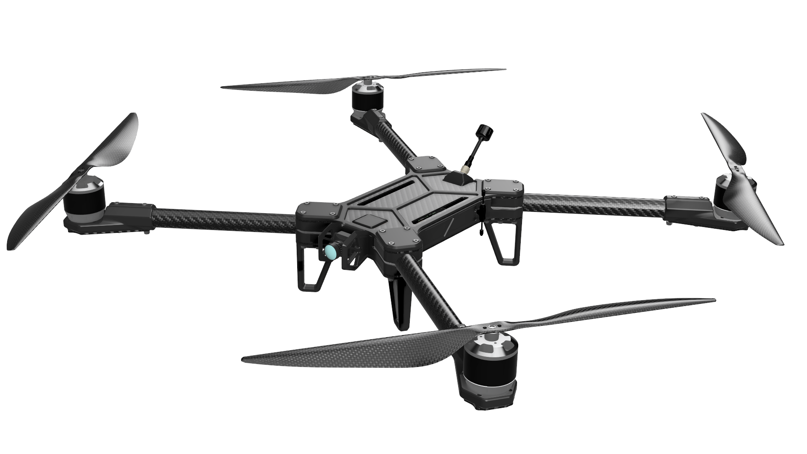
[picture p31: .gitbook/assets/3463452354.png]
<figure><figcaption></figcaption></figure>

**Compatible Models**: Genesis, Genesis-Bravo, Genesis-M

FPV or First Person View, allows

## Digital FPV

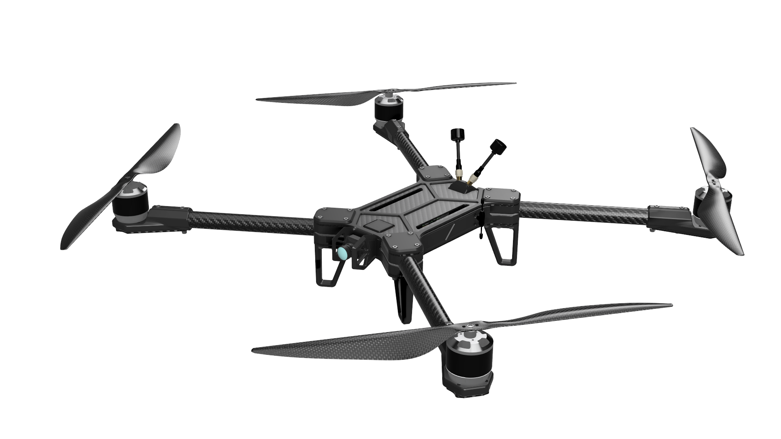
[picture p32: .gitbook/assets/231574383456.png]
<figure><figcaption></figcaption></figure>

**Compatible Models:** Genesis, Genesis-Bravo, Genesis-M

## R\&D

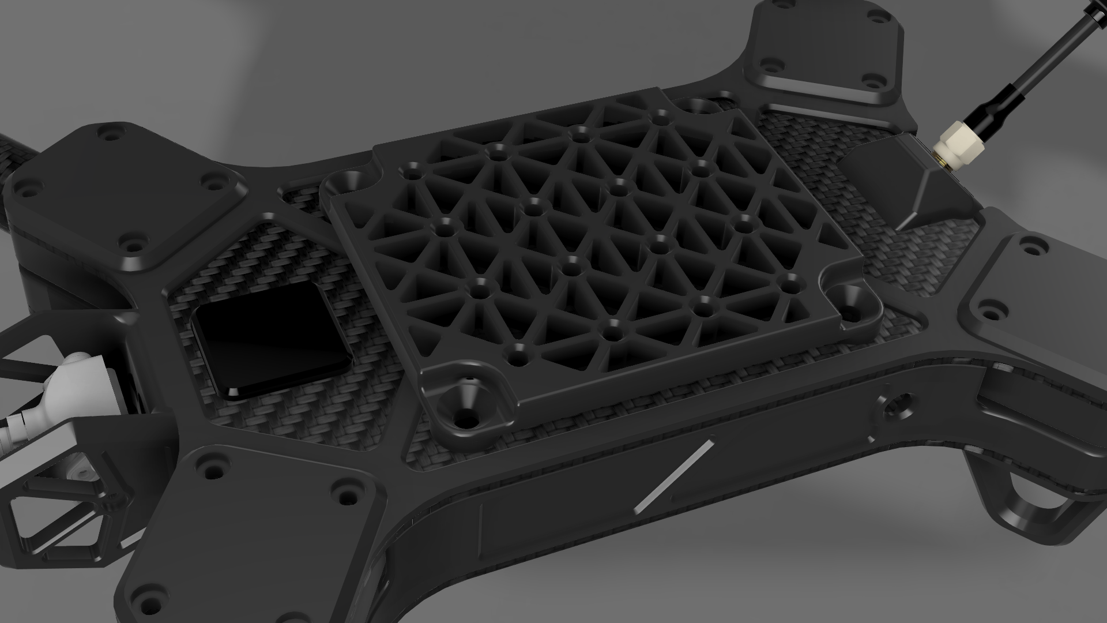
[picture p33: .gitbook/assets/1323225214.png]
<figure><figcaption></figcaption></figure>

**Compatible Models:** Genesis, Genesis-Bravo, Genesis-M

k

## Onboard Autonomy

## ISR

Coming soon.

**Compatible Models:** Genesis-Bravo, Genesis-M

## Terminal Guidance

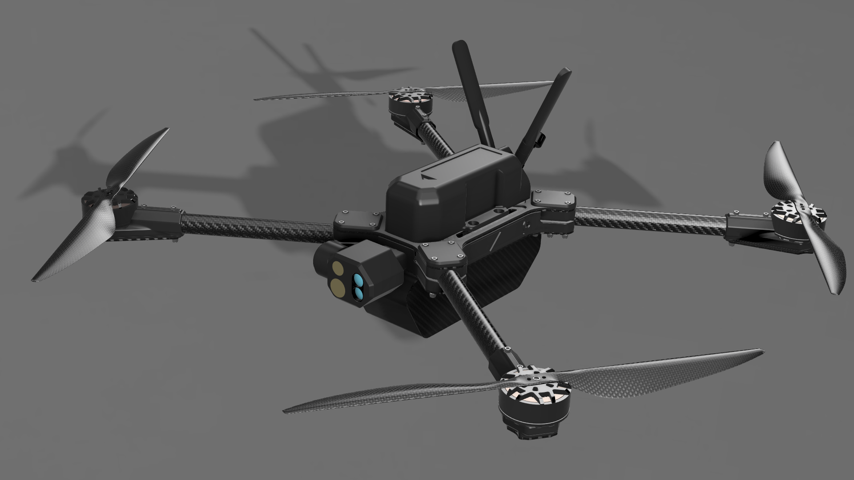
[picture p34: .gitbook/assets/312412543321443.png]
<figure><figcaption></figcaption></figure>

**Compatible Models:**  Genesis-M

Only available on Genesis-M for government customers. More details will be available soon. Contact us here.

## Custom Configuration

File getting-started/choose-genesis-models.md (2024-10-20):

---
hidden: true
cover: ../.gitbook/assets/3421431324 (1).png
coverY: 0
---

# Choose Genesis Models

The Genesis drone family comes in three variants. Select the variant that matches your application or mission set below.

## Genesis

<figure><figcaption></figcaption></figure>

Genesis is the most economical, manufacturable, and accessible variant of aimed for beginner drone builders. Genesis is easy to build with very few tools or resources required. Being electronics agnostic, users can select and source various motors, flight controllers, and more from a diverse range of suppliers. Genesis is designed to be simple, reliable, and accessible.

{% hint style="info" %}
Genesis-A is the most economical option and is recommended for most builders.
{% endhint %}

### Links:

#### [Genesis-A Docs](../genesis/part-chooser/)&#x20;

#### Buy Kits

## Genesis-Bravo (NDAA Compliant)

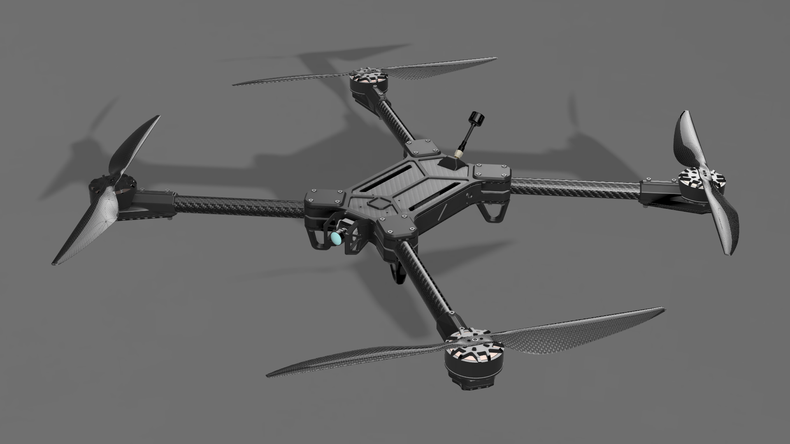
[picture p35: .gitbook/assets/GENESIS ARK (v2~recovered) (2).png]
<figure><figcaption></figcaption></figure>

The Bravo model is for both civilian and defense professionals, with more smarter feature. Genesis-B is powered by

## Genesis-M (NDAA Compliant, Munition)

<figure><figcaption></figcaption></figure>

The Genesis-M is designed for terminal guidance applications, tactical ISR, and other multi-mission roles. Genesis-M is in active developing for government customers. Genesis-M is only available for government and military customers. For procurement or development details, please reach out to us.&#x20;

### Links:

#### Contacts

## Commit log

2024-09-09 GITBOOK-10: No subject
    [Genesis Arm Mount.3mf, Genesis FPV Camera Mount.3mf, Genesis Landing Gear.3mf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]
2024-09-09 GITBOOK-26: No subject
    [Airframe Bottom.dxf, Airframe Bottom.step, Airframe Top.dxf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]
2024-09-11 GITBOOK-41: No subject
    [Arm Alignment Tool.3mf]
2024-09-25 GITBOOK-54: No subject
    [Battery Mount.3mf]
2024-09-26 GITBOOK-57: No subject
    [Rubber Stencil Tool.3mf]
2024-10-16 GITBOOK-113: No subject
    [Landing Gear Extended v1.step]
2024-10-19 GITBOOK-128: No subject
    [Genesis Landing Gear (1).3mf]
2024-10-20 GITBOOK-137: No subject
    [Genesis Main Body Digital FPV.3mf]
2024-10-22 GITBOOK-145: No subject
    [Battery Mount (1).3mf]
2024-10-26 GITBOOK-150: No subject
    [Arm Alignment Tool (1).3mf, Arm Alignment Tool.3mf]
2024-11-04 GITBOOK-192: No subject
    [Battery Mount (2).3mf]
2024-11-04 GITBOOK-193: No subject
    [Digital FPV Camera Mount.3mf]
2024-11-21 GITBOOK-215: No subject
    [arm alignment tool v2.step]
